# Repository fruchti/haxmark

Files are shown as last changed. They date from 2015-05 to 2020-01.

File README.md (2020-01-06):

# haxmark

This project has the goal of modifying a Lexmark E360d/E360dn for direct PCB printing.

It is based on [this](http://www.instructables.com/id/Modification-of-the-Lexmark-E260-for-Direct-Laser--1) great instructable by mlerman, which uses a Lexmark E260d. The E360d is nearly identical in its hardware. Anyhow, I found out that there are some software differences between E260d and E360d. This is why a designed a new MCU board for simulating the printer's timings.

## Project status and performance

The printer behaves reasonably predictable and the way it should. The results are quite good: A minimal trace width of 5 mil and a minimal clearance of 10 mil are no big deal.

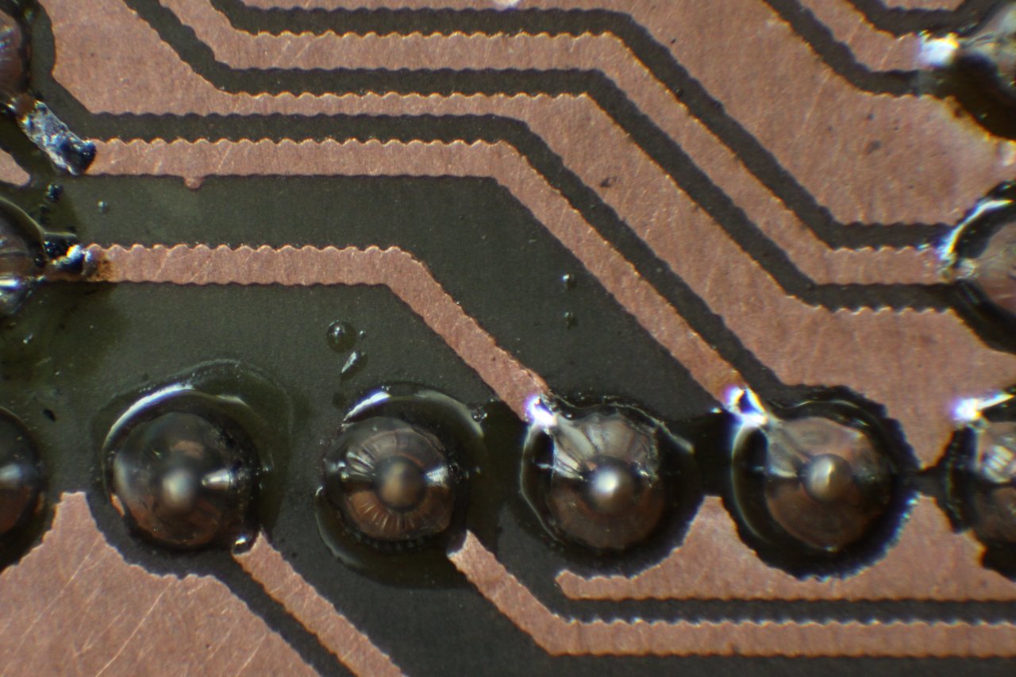
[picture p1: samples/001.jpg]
MCU Board


A review of the project and some potential issues of the process in general can be found in [a blog post of mine](https://25120.org/post/haxmark/).

## Modification

### Some notes before you modify your printer

I strongly recommend that you test your printer in an unmodified state with exactly the driver and printer settings you intend to use it with to print on PCBs. I found out the hard way that the behaviour and the timing differ from driver to driver. It is definitely a good idea to make a dump of the interesting signals (operator panel line, manual paper feed sensor, paper in sensor, exit sensor) with a logic analyser to get the exact timing of your printing setup so you can adjust the timing settings in the MCU board's source code. I included a dump made with logic_sniffer and my settings. I use the printer with linux and [this](http://www.openprinting.org/printer/Lexmark/Lexmark-E360d) PPD file with 1200dpi native resolution. I have not used it with Windows, so if you plan to do that, better check the printer's behaviour in detail before making any modification.

### Differences to the E260d

The main hardware difference between E260d and E360d is the use of a different operator's panel. But in the software there seem to be quite some more:

- The E360d does not, unlike the E260d, pull in a piece of paper stuck into its front. Instead, it stops with a paper jam message.
- When starting a print, the printers motor runs for a while before it is stopped and the user has to confirm he has inserted a piece of paper into the manual feeder by pressing the tick button. Then, the motor starts running again and a few seconds later, a clutch is activated and the paper is finally pulled in. If the paper is inserted significantly before the clutch is activated, the printer reports a paper jam. Note that some drivers seem to omit the first motor running phase (this modification should work with both variants)

### Hardware modification

The hardware modifications are mainly the same as in [the original instructable](http://www.instructables.com/id/Modification-of-the-Lexmark-E260-for-Direct-Laser--1). But, because the motor directly pulls in the carrier, an additional clutch is needed to keep the rollers stopped unless the carrier actually should move. The printer provides a solenoid, which is able to block the rollers, on its left side. Cut the low-side cable at the printer's controller board and connect it to the new MCU board. Leave the other end connected to 24 V. The MCU board also needs a connection to a hall sensor of the motor in order to be able to check if it is running. I tapped the lowest pin on J17, but any of the three sensor lines should work. Just be sure that you do not connect the MCU to one of the motor windings (the three wires with the ferrite bead over them), as they are driven with 24 V.

I made some additional modifications:

- I use a 18 cm wide and 30 cm long carrier. The 60 cm long carrier proved to be way to long for me.
- I swapped the forked light barrier "new paper in sensor" for a reflective sensor (SFH900-2). This way I can use a piece of tape on the carriers bottom instead of a hole. If you use the original approach, you have to invert the signal in the AVR's source code.
- My carrier has two markings for the reflective light sensor. The new first marking triggers the sensor when the carrier is pulled in just slightly. The MCU board uses this to feed the carrier into the printer into the exact same starting position every time. Especially for double-sided PCBs this is useful as it provides better alignment. The markings on my carrier are now 113 mm and 181 mm from the top with the reflective light sensor being 100 mm in front of the first axle.

### New MCU board

My new controller board monitors the motor in addition to the tapped line from the operator panel, which by the way is a serial data line and gets toggled with every key press, at the startup and every once in a while. I also included three status LEDs, which are not really useful at the moment, and an RS232-TTL port for debugging purposes, which is unused so far. The crystal is actually optional, just make sure you change the fuse bits in the makefile if you do not solder one in.

## Printing

The printing process is straightforward:

1. Hit "Print" in whatever program you design your PCBs with
2. Wait until the printer's motor stops running
3. Put the carrier with the bare PCB on it in
4. Press the tick button on the printer and watch it print
5. Treat the PCB in acetone vapour (as described in the original instructable) and etch

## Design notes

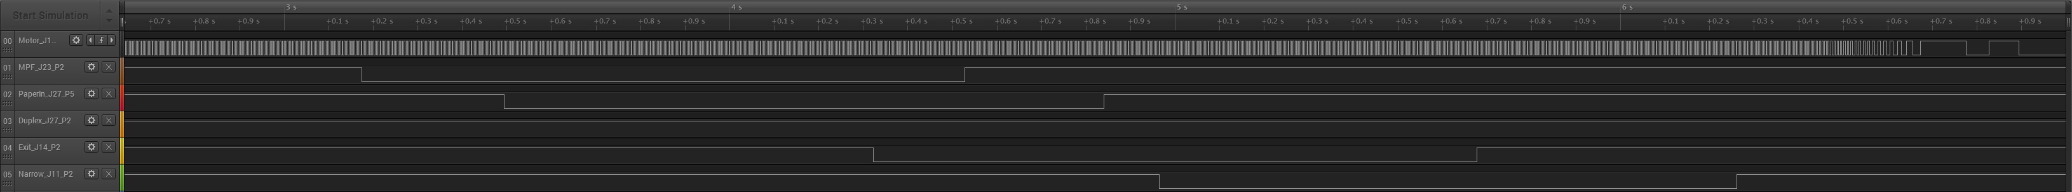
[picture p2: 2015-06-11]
ols-dumps/Win7_AHC_Admin_XL_Desktop_NET.jpg

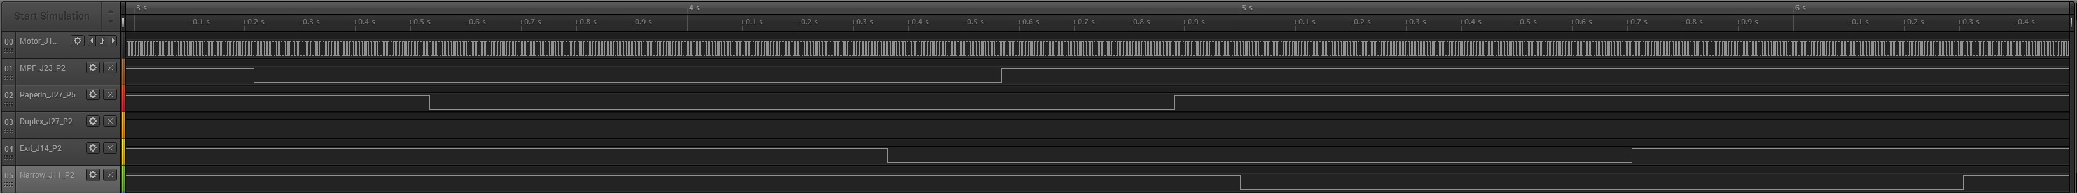
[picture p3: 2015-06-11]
ols-dumps/Win7_Generic_DRV_Desktop_NET.jpg

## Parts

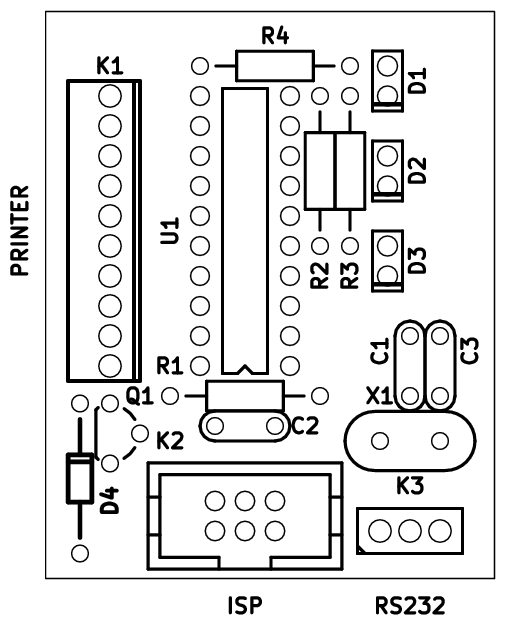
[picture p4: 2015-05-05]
kicad/components.png

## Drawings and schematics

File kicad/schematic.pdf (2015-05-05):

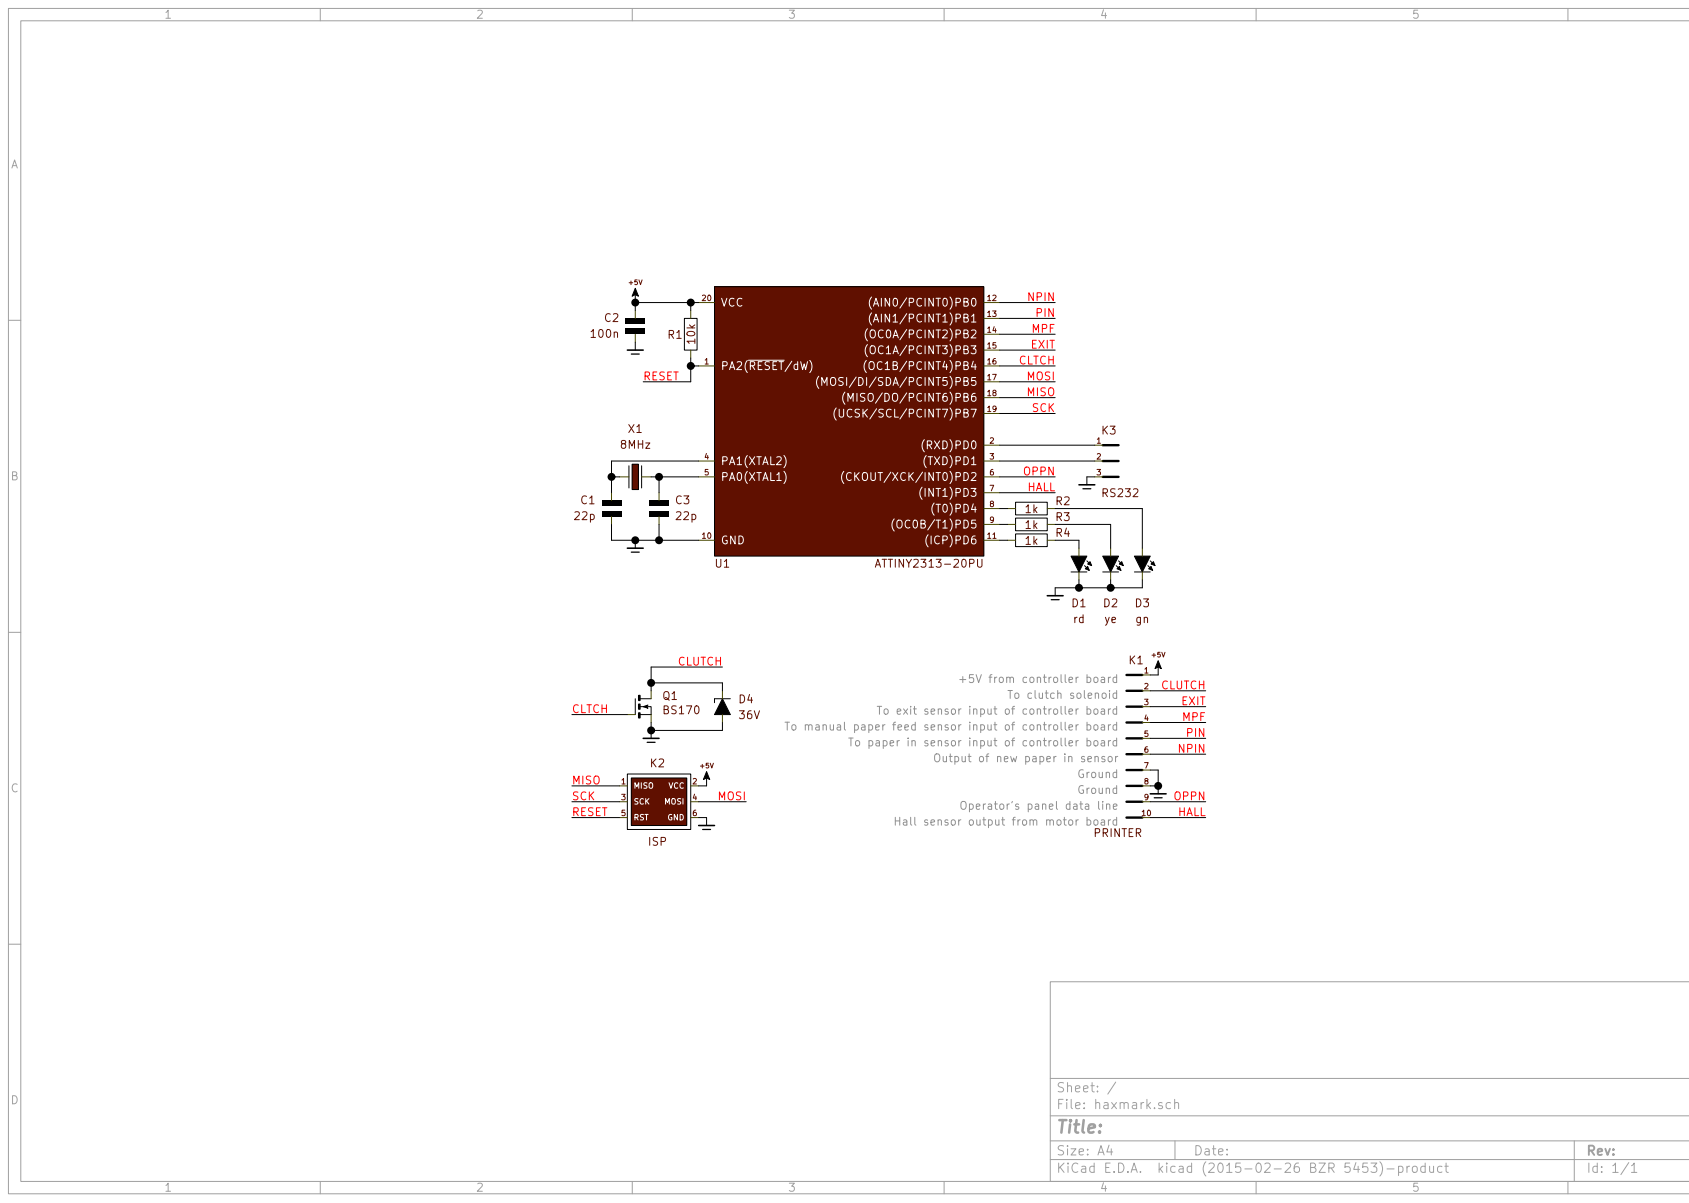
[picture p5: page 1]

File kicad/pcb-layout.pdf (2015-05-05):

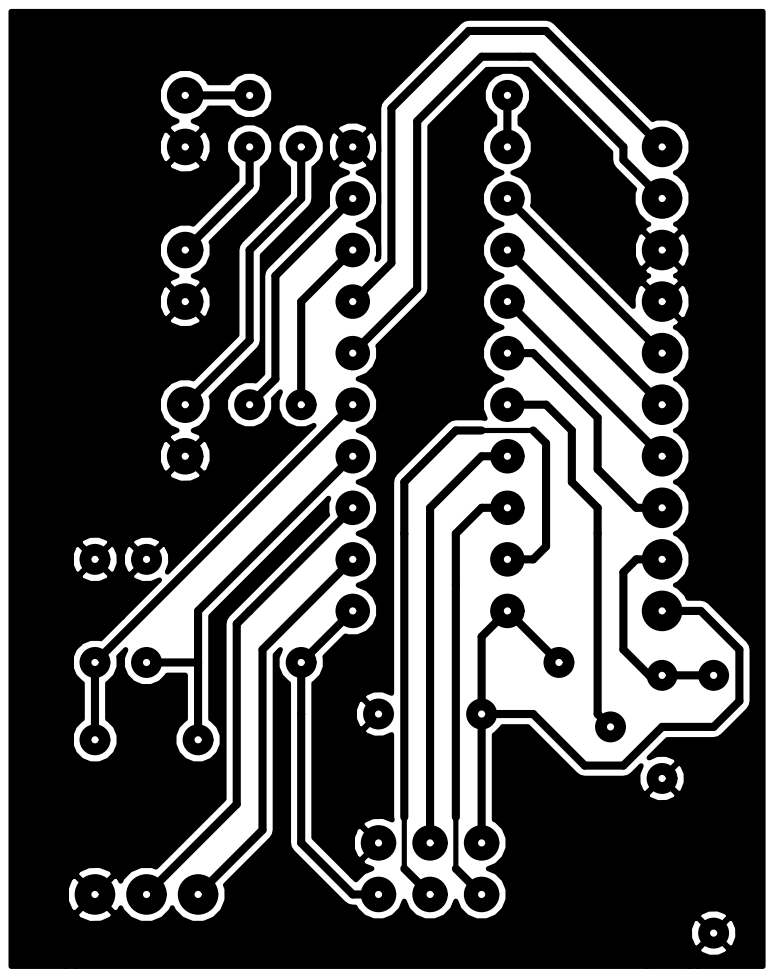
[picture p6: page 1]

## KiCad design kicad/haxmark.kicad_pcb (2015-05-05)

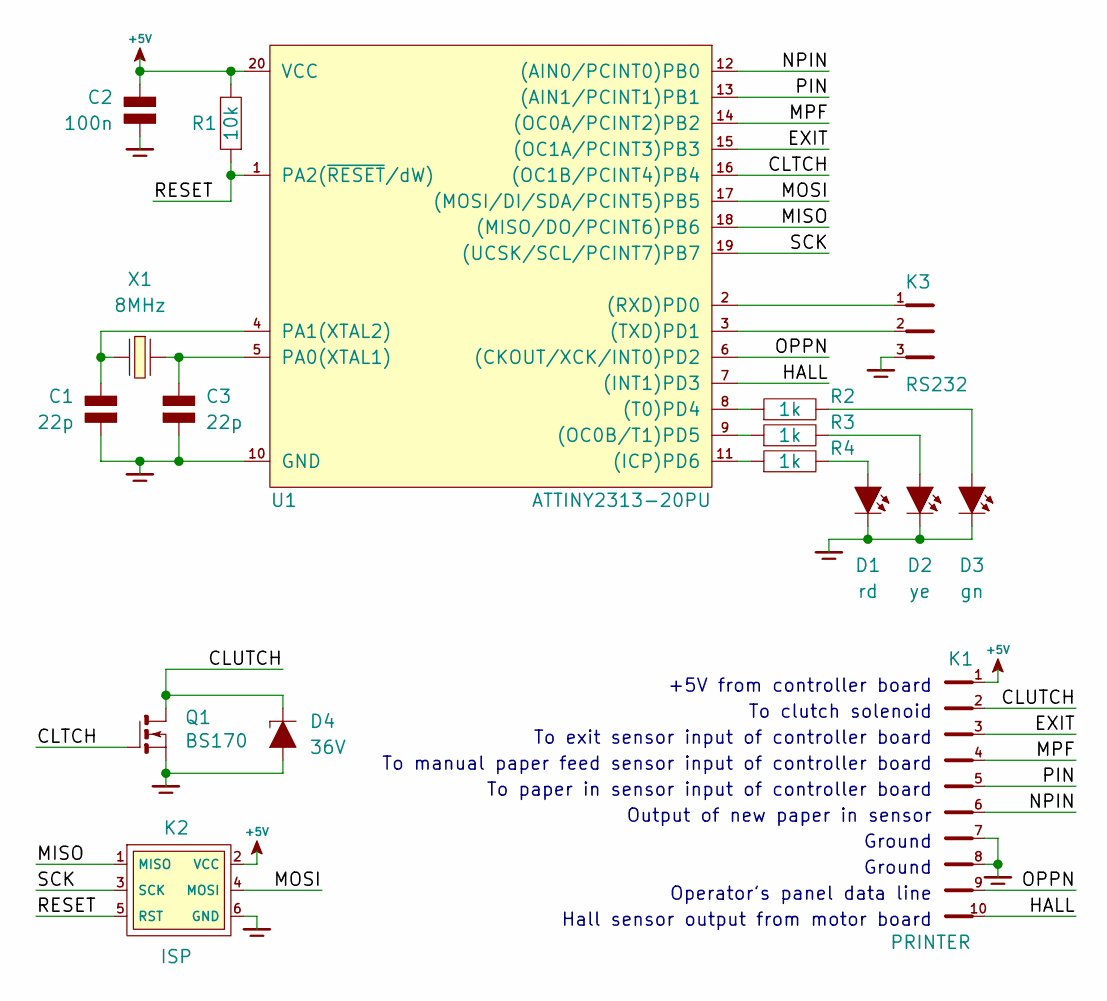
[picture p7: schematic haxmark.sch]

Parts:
C1, C3: 22p; C_200
C2: 100n; C_200
D1: rd; LED_RECT
D2: ye; LED_RECT
D3: gn; LED_RECT
D4: 36V; DO35_500
K1: PRINTER; PSS254-10G
K2: ISP; WSL6G
K3: RS232; PINHEAD_1_3
Q1: BS170; TO92
R1: 10k; R_0207_500
R2, R3, R4: 1k; R_0207_500
U1: ATTINY2313-20PU; DIP20_300
X1: 8MHz; XTAL_200

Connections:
+5V: C2.1, K1.1, K2.2 (VCC), R1.2, U1.20 (VCC)
/CLTCH: Q1.2 (G), U1.16 ((OC1B/PCINT4)PB4)
/CLUTCH: D4.2 (C), K1.2, Q1.1 (D)
/EXIT: K1.3, U1.15 ((OC1A/PCINT3)PB3)
/HALL: K1.10, U1.7 ((INT1)PD3)
/MISO: K2.1 (MISO), U1.18 ((MISO/DO/PCINT6)PB6)
/MOSI: K2.4 (MOSI), U1.17 ((MOSI/DI/SDA/PCINT5)PB5)
/MPF: K1.4, U1.14 ((OC0A/PCINT2)PB2)
/NPIN: K1.6, U1.12 ((AIN0/PCINT0)PB0)
/OPPN: K1.9, U1.6 ((CKOUT/XCK/INT0)PD2)
/PIN: K1.5, U1.13 ((AIN1/PCINT1)PB1)
/RESET: K2.5 (RST), R1.1, U1.1 (PA2(~RESET~/dW))
/SCK: K2.3 (SCK), U1.19 ((UCSK/SCL/PCINT7)PB7)
GND: C1.2, C2.2, C3.2, D1.2 (C), D2.2 (C), D3.2 (C), D4.1 (A), K1.7, K1.8, K2.6 (GND), K3.3, Q1.3 (S), U1.10 (GND)
unnamed: C1.1, U1.4 (PA1(XTAL2)), X1.2
unnamed: C3.1, U1.5 (PA0(XTAL1)), X1.1
unnamed: D1.1 (A), R4.2
unnamed: D2.1 (A), R3.2
unnamed: D3.1 (A), R2.2
unnamed: K3.1, U1.2 ((RXD)PD0)
unnamed: K3.2, U1.3 ((TXD)PD1)
unnamed: R2.1, U1.8 ((T0)PD4)
unnamed: R3.1, U1.9 ((OC0B/T1)PD5)
unnamed: R4.1, U1.11 ((ICP)PD6)

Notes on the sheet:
+5V from controller board
Hall sensor output from motor board
Operator's panel data line
Ground
Output of new paper in sensor
To paper in sensor input of controller board
To manual paper feed sensor input of controller board
To exit sensor input of controller board
To clutch solenoid

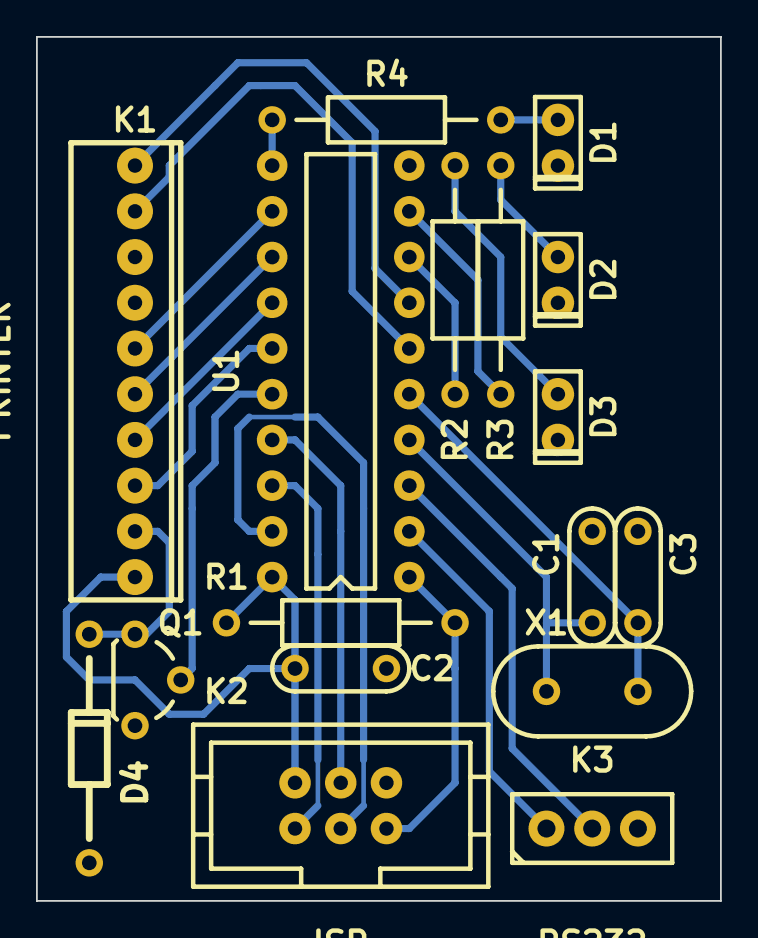
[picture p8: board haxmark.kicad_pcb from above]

Board: 2 copper layers, 38.0 x 48.0 mm, 17 parts (0 on the bottom side), 24 nets.

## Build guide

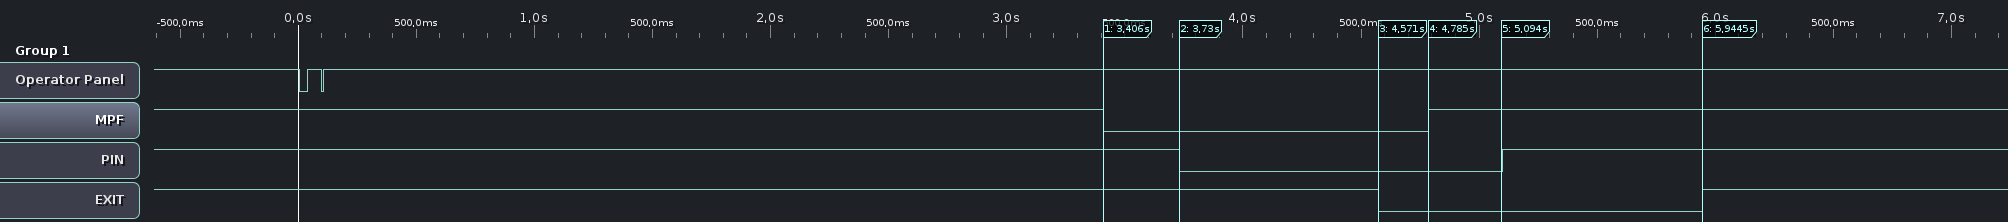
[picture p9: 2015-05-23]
ols-dumps/unmodified-a4-manual-2400dpi-image-linux.png

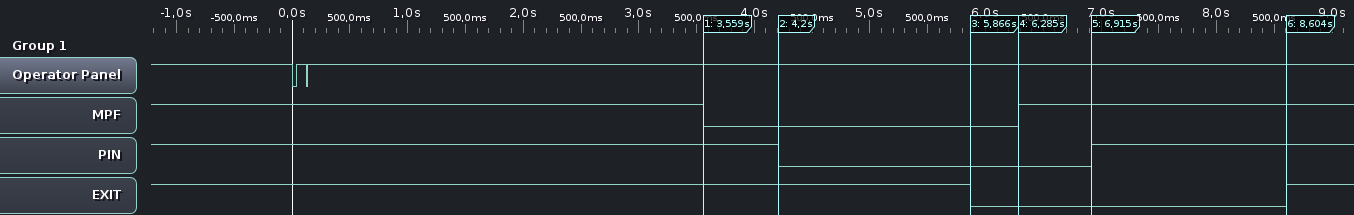
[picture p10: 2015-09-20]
ols-dumps/unmodified-a4-manual-1200dpi-native-linux.png

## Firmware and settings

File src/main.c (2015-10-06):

// -fruchti 2015

#include "main.h"

volatile uint32_t MillisecondCounter = 0;
volatile uint16_t HallSensorTimer = T_HALL_L;
volatile State_t State = PowerOnWait;
volatile uint8_t HallSensorBuffer = 0;

int main(void)
{
    //// IN- AND OUTPUTS ////

    D_LED_RD |= (1 << P_LED_RD);
    D_LED_YE |= (1 << P_LED_YE);
    D_LED_GN |= (1 << P_LED_GN);
    O_LED_RD |= (1 << P_LED_RD);
    O_LED_YE |= (1 << P_LED_YE);
    O_LED_GN |= (1 << P_LED_GN);
    O_NPPINS |= (1 << P_NPPINS);
    O_PPINSO |= (1 << P_PPINSO);
    D_PPINSO |= (1 << P_PPINSO);
    O_MNPFSO |= (1 << P_MNPFSO);
    D_MNPFSO |= (1 << P_MNPFSO);
    O_EXITSO |= (1 << P_EXITSO);
    D_EXITSO |= (1 << P_EXITSO);
    D_CLUTCH |= (1 << P_CLUTCH);
    O_CLUTCH |= (1 << P_CLUTCH);


    //// TIMER 0 ////

    // Enable CTC mode
    TCCR0A = (1 << WGM01);
    // Select clock F_CPU/64 (125kHz)
    TCCR0B = (1 << CS01) | (1 << CS00);
    // 1kHz interrupt frequency
    OCR0A = 124;

    // Enable OC0A interrupt
    TIMSK = (1 << OCIE0A);


    //// EXTERNAL INTERRUPTS ////

    // Trigger on the falling edge for operator panel input
    MCUCR |= (1 << ISC01);
    // Enable external interrupt 0
    GIMSK |= (1 << INT0);

    // Trigger on both edges for hall sensor input
    MCUCR |= (1 << ISC10);
    // Enable external interrupt 1
    GIMSK |= (1 << INT1);

    sei();

    MillisecondCounter = 0;
    State = PowerOnWait;

    while(1)
    {
        switch(State)
        {
            case PowerOnWait:
                // Does nothing.
                // Waits for the initialization of the printer to complete
                if(MillisecondCounter >= T_POWRON)
                {
                    State = Idle;
                }
                break;
            case Idle:
                // Activate clutch and reset all sensor output just in case
                // something has gone mucus
                O_PPINSO |= (1 << P_PPINSO);
                O_MNPFSO |= (1 << P_MNPFSO);
                O_EXITSO |= (1 << P_EXITSO);
                O_LED_RD |= (1 << P_LED_RD);
                O_CLUTCH &= ~(1 << P_CLUTCH);
                O_LED_GN &= ~(1 << P_LED_GN);

                // Check if motor is running and new paper in sensor is
                // blocked by carrier
                if(HallSensorTimer < T_HALL_L && !(I_NPPINS & (1 << P_NPPINS)))
                {
                    // Unblock carrier
                    O_CLUTCH &= ~(1 << P_CLUTCH);
                    O_LED_GN |= (1 << P_LED_GN);
                    O_LED_RD &= ~(1 << P_LED_RD);

                    State = AlignFeed;
                }
                break;
            case AlignFeed:
                // Check if carrier has moved to the first marked position
                if(I_NPPINS & (1 << P_NPPINS))
                {
                    // Block carrier
                    O_CLUTCH |= (1 << P_CLUTCH);

                    State = ClutchDelay;
                    MillisecondCounter = 0;
                }
                break;
            case ClutchDelay:
                if(MillisecondCounter >= T_CLUTCH)
                {
                    // Deactivate clutch to allow carrier to get pulled in
                    O_CLUTCH &= ~(1 << P_CLUTCH);

                    // Enable manual paper feed sensor
                    O_MNPFSO &= ~(1 << P_MNPFSO);

                    State = WaitingForFeed;
                }
                break;
            case WaitingForFeed:
                // Check if the end of the alignment marking on the carrier is
                // hit (this state is needed because the alignment marking would
                // lead to skipping the WaitingForPaperIn state right away)
                if(!(I_NPPINS & (1 << P_NPPINS)))
                {
                    State = WaitingForPaperIn;
                }
                break;
            case WaitingForPaperIn:
                // Check if paper in sensor is triggered
                if(I_NPPINS & (1 << P_NPPINS))
                {
                    // Enable paper in sensor output
                    O_PPINSO &= ~(1 << P_PPINSO);
                    O_LED_RD |= (1 << P_LED_RD);

                    MillisecondCounter = 0;
                    State = ExitOnDelay;
                }
                break;
            case ExitOnDelay:
                if(MillisecondCounter >= T_EXIT_H)
                {
                    // Activate exit sensor output
                    O_EXITSO &= ~(1 << P_EXITSO);

                    MillisecondCounter = 0;
                    State = ManualPaperFeedOffDelay;
                }
                break;
            case ManualPaperFeedOffDelay:
                if(MillisecondCounter >= T_MNPF_L)
                {
                    // Deactivate manual paper feed sensor output
                    O_MNPFSO |= (1 << P_MNPFSO);

                    MillisecondCounter = 0;
                    State = PaperInOffDelay;
                }
                break;
            case PaperInOffDelay:
                if(MillisecondCounter >= T_PPIN_L)
                {
                    // Deactivate paper in sensor output
                    O_PPINSO |= (1 << P_PPINSO);

                    MillisecondCounter = 0;
                    State = ExitOffDelay;
                }
            case ExitOffDelay:
                if(MillisecondCounter >= T_EXIT_L)
                {
                    // Deactivate exit sensor output
                    O_EXITSO |= (1 << P_EXITSO);

                    MillisecondCounter = 0;
                    State = Idle;
                }
                break;
        }
    }
}

ISR(TIMER0_COMPA_vect)
{
    MillisecondCounter++;
    if(MillisecondCounter == 0)
    {
        MillisecondCounter = UINT32_MAX;
    }

    if(State != PowerOnWait)
    {
        HallSensorTimer++;
        if(HallSensorTimer == 0)
        {
            HallSensorTimer = UINT16_MAX;
        }
        if(HallSensorTimer < T_HALL_L)
        {
            O_LED_YE |= (1 << P_LED_YE);
        }
        else
        {
            O_LED_YE &= ~(1 << P_LED_YE);
        }
    }
}

// External interrupt. Triggered by control panel
ISR(INT0_vect)
{
    // Just reset everything
    if(State == WaitingForPaperIn || State == ClutchDelay)
    //if(State != PowerOnWait)
    {
        State = Idle;
    }
}

// External interrupt. Triggered by hall sensor
ISR(INT1_vect)
{
    HallSensorTimer = 0;
}

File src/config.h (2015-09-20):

// -fruchti 2015

#ifndef CONFIG_H_
#define CONFIG_H_

#define F_CPU           8000000

#include <avr/io.h>
#include <avr/interrupt.h>

// Printer settings
#define PRINTRES        1200            // Resolution, either 1200 or 2400 (dpi)

// All delay times are measured in milliseconds
#define T_HALL_L        6               // Hall sensor timeout. After this time
                                        // is elapsed without a pin change, the
                                        // motor is considered stopped
#define T_POWRON        5000            // Delay to allow printer to start up

#if PRINTRES == 1200                    // Printer set to 1200dpi

#define T_CLUTCH        3559            // Delay between starting print job and
                                        // pulling in carrier/activating manual
                                        // paper feed sensor
#define T_EXIT_H        1666            // Delay between activation of paper in
                                        // and activation of exit sensor
#define T_MNPF_L        419             // Delay before deactivation of manual
                                        // paper feed sensor after exit sensor
                                        // is activated
#define T_PPIN_L        630             // Delay before deactivation of paper
                                        // in sensor
#define T_EXIT_L        1689            // Delay before deactivation of exit
                                        // sensor

#else                                   // Timing for 2400dpi image resolution
#define T_CLUTCH        3406
#define T_EXIT_H        841
#define T_MNPF_L        213
#define T_PPIN_L        311
#define T_EXIT_L        849
#endif

#define D_LED_RD        DDRD            // Red status LED
#define O_LED_RD        PORTD
#define P_LED_RD        PD6

#define D_LED_YE        DDRD            // Yellow status LED
#define O_LED_YE        PORTD
#define P_LED_YE        PD5

#define D_LED_GN        DDRD            // Green status LED
#define O_LED_GN        PORTD
#define P_LED_GN        PD4

#define I_NPPINS        PINB            // New paper in sensor
#define O_NPPINS        PORTB
#define P_NPPINS        PB0

#define D_PPINSO        DDRB            // Paper in sensor output
#define O_PPINSO        PORTB
#define P_PPINSO        PB1

#define D_MNPFSO        DDRB            // Manual paper feed sensor output
#define O_MNPFSO        PORTB
#define P_MNPFSO        PB2

#define D_EXITSO        DDRB            // Exit sensor output
#define O_EXITSO        PORTB
#define P_EXITSO        PB3

#define D_CLUTCH        DDRB            // Clutch control pin
#define O_CLUTCH        PORTB
#define P_CLUTCH        PB4

#define I_OPANEL        PIND            // Operator panel
#define P_OPANEL        PD2             // CAUTION: Do not change (INT0 is used
                                        // for monitoring this input)!

#define I_HALL_1        PIND            // Hall sensor from motor
#define P_HALL_1        PD3

#endif

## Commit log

2015-05-23 Always complete sensor signal sequence when started
    I started getting paper jam errors which was likely to be caused by
    communication between printer controller board and operator's panel
    toggling the tapped data line and therefore resetting the MCU board's
    state to the idle state while printing. If the state is reset before the
    signal sequence is completed, the printer of course will not get the
    sensor signals it is expecting.
    The line had been commented out because it had caused some weird
    problems in the past. For example, my printer now needs a hard reset
    after each print because it refuses to print a second time. As I think
    not being able to print at all is worse than that, I put the l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
    [main.c]
2015-06-11 Win7 Logic dumps added
    Pictures and CSV of logic level dumps of an unmodifed E360DN added.
    Legacy Win7 driver and Lexmark driver captured
    [Win7_AHC_Admin_XL_Desktop_NET.csv, Win7_AHC_Admin_XL_Desktop_USB.csv, Win7_Generic_DRV_Desktop_NET.csv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]
2015-09-20 Drive clutch at startup
    Now you can directly hear if everything is working when turning the printer on.
2015-09-20 Add logic analyzer dump of 1200dpi print
2015-09-20 Adjust timing to 1200dpi
    At first I was using the 2400dpi mode of the printer. I now switched to
    the native resolution of 1200dpi because the results are way better. The
    2400dpi mode can still be used if a #define in config.h is changed.
2015-10-06 Add initial feed
    The MCU board now lets the printer pull in the carrier until the new
    paper in sensor is triggered for the first time and then starts the
    print like before. The new "initial feed" provides an alignment of the
    carrier which is exactly the same every time. Of course, the carrier now
    needs two markings.
